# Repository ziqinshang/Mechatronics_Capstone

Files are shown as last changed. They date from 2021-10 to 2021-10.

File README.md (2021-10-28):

# Mechatronics_Capstone
## Overview
### This is a 4th year mechatronics engineering capstone project, The function of the device is to autonomously navigate a tomato or cherry tomato in greenhouse, and identify, pick, and collect tomatoes. This task was decomposed into several subsystems, navigation, image processing and robotic manipulation.
## Prototyping in Solidworks
CAD1
CAD2
## Frame Structure
Frame Structure 1
Frame Structure 2
## Manipulator Structure
Manipulator Structure
#### Note
#### Due to COVID-19 pandemic, several components necessary to finalize the development of the device were not fabricated resulting in a less-than-fully-functional prototype despite promising test data.
#### Group Effort
#### Credit: Alexander Cleator,Mingyang Xu, Qi Qi

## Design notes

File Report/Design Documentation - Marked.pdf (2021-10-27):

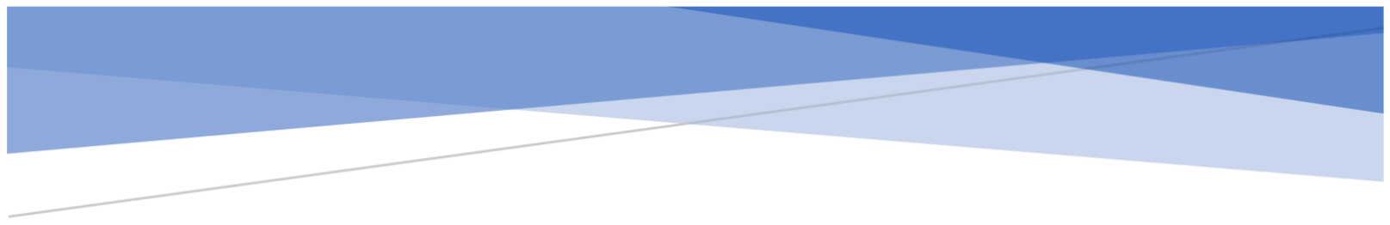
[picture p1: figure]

# FRUIT PICKING ROBOT FINAL DESIGN DOCCUMENTATION

## Group 7

Submitted: Feb 25, 2020

Prof. A. Samani

Alexander Cleator
Ziqin Shang
Qi Qi
Mingyang Xu

FRUIT PICKING ROBOT FINAL DESIGN DOCCUMENTATION | 1

## Table of Contents

# Part1: Design Analysis

## Frame Analysis

The frame is made from extruded 1060 aluminum alloy beams with following material

properties found on CES 2019:

Table 1: 1060 Aluminum Properties

1060 Aluminum is a strong, lightweight material that suitable for various of applications, in this

application, the strength of aluminum fulfilled the design requirement of supporting approximately 5kg of fruit and the 10kg mass of the robot. An FEA analysis was

conducted with a loading scenario of 100N distributed force on the base plate, a fine mesh was used in

this analysis. The results of the FEA analysis are shown in the following figures.

Figure 1: Von Mises Stress

It was found that the maximum Von Mises stress occurs on the contact edge of the plate and

the frame, which is 2.057 MPa, the yield strength of 1060 aluminum is approximately 160 MPa,

indicating no risk of failure by yielding.

The resultant displacement from the same analysis is shown below; it was found that the

maximum displacement of 0.03mm occurred along the center line of the plate.

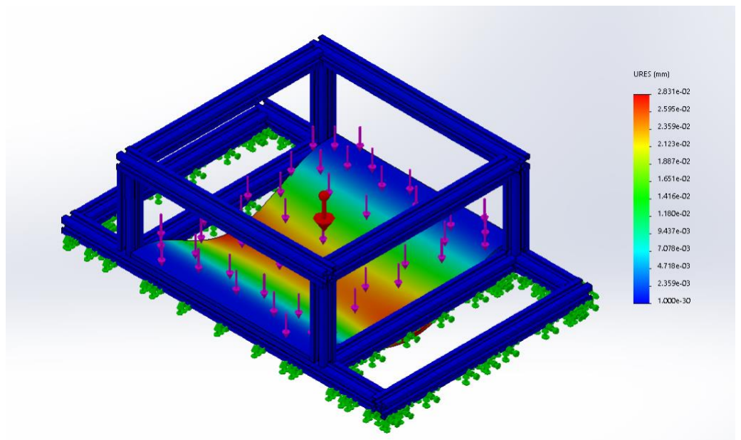
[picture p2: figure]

Figure 2: Deflection

## Motor analysis

By estimating the mass of the robot to be 10kg, a normal force of 24.5N can be applied

to each of the four wheels. Assuming the frictional coefficient between the wheels and the

ground is 0.6, a frictional force of 14.7N must be overcome. Based on Newton’s second law, a

net force of 1N must be applied to allow the 10kg device to accelerate at a rate of 0.1 m
s

2

Disregarding the moment of inertia of the wheel (as it was determined to be

inconsequential), the required torque can be calculated as follows:

τ = F x r = (15.7N) x (0.09m) = 1.41 Nm

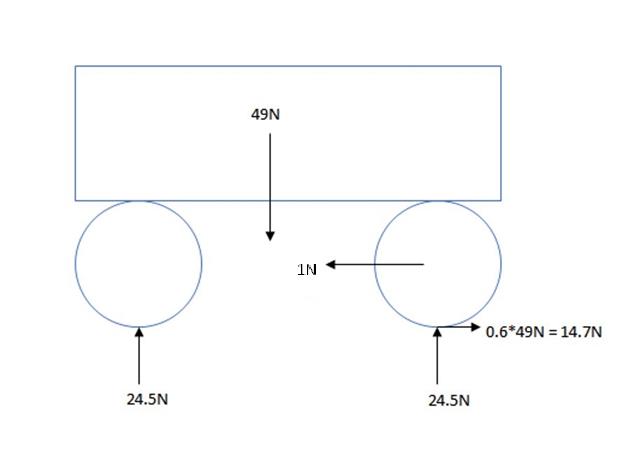
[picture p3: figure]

Figure 3: Chassis Static Force Analysis

Equating the applied force and friction, the required torque for continuous velocity can be

determined as follows.

τsteady state = Ffriction × rwℎeel = 14.7N × 0.09m = 1.32Nm

By estimating the operational speed of 0.5m
s

, the required rotational speed can be calculated

using the diameter of the wheel and speed of the robot:

circ. = πd = 0.18m x π = 0.565m

f =

v
circ

. =

0.5m
s
0.565m

= 0.884 Hz

frpm = 60f = 60(0.884) = 53 rpm

Considering the limited budget, a brushed DC motor is the optimal solution.

In this application, a gearbox is required because of the high speed, low torque direct output

from the motor.

Based on the specification that the selected motor must have a stall torque under 1.4 Nm and a

rated torque ideally as close as possible to 1.3Nm to maximize mechanical efficiency, a gearbox motor

with the following properties was selected.

Table 2: DC Motor Properties

Voltage | No-load speed | Rated speed | Rated torque | No-load current | Rated current | Stall current
24V DC | 325±30 RPM | 230 ± 20 RPM | 1.324N.m | 0.3A | 2.3A | 7A

The motor has an integrated 1:27 gear reducer, which amplifies the rated torque from 50mNm

to 1.324Nm that will fulfill the design requirement. A CNC machined steel shaft mount with an

integrated bearing was also purchased to mount the motor on the chassis. A 180mm diameter wheel

with aluminum wheel hub and rubber tire will be attached to the motor assembly.

The motor can be controlled using pulse width modulation, after a series of tests, a 15VDC

supply, operating at a 30% duty cycle could achieve the specified rate of 0.5 m
s

, a peak speed of 2.7m
s

was

observed during testing, which would be implemented if not for safety considerations. For this device,

rear differential steering was used due to the potential for zero-turn-radius steering. After completing

the concept generation and selection phases of the design development, construction began on both

a physical prototype and a Solidworks assembly to model the completed concept.

## Navigational System analysis

The navigational system uses an 8-bit hall-effect based magnetic line tracker and a 1.5-inch

magnetic strip. The magnetic tape is to be adhered to ground and line tracking sensor will detect

the horizontal relative location of the tape. By inputting the location information into a microprocessor

and using if-then logic, the speed of the two motor can be effectively controlled.

The magnetic sensor communicates serially based on MODBUS-RTU communication protocol or

as well as outputting the states of each of the hall-effect sensors NPN open-drain configurations. After

having difficulty establishing communication with the sensors MODBUS, tracking was achieved by

polling each of the sensors independently. Using the internal pull-up resistors in the

microprocessor, this information can be read directly through corresponding digital pins. After

processing, the microprocessor outputs a 5V PWM signal, which is amplified to a nominal voltage using

an integrated motor driver.

After a series of tests with different duty cycles and nominal voltages, following test results were

measured.

Table 3:Driving Speed Testing

Nominal Voltage | PWM ratio | Speed
10V | 30% | 0.3m/s
10V | 80% | 0.85m/s
15V | 30% | 0.5m/s
15V | 60% | 1m/s
24V | 30% | 0.8m/s
24V | 100% | 2.7m/s

Based on the test results, it was found that the robot can travel at a maximum speed of 2.7m
s

. By

varying the nominal voltage and duty cycle, the speed of robot can vary from 0.3 m
s

to 2.7 m
s

. The device

was unable to drive if the nominal voltage applied was less than 10V irrespective of duty cycle, voltages

above 24V were not tested to avoid potential damage to the motors being tested.

## 5 Degree of Freedom Manipulator

The manipulator operates using open loop controllers for each of the joints, which were coded

by the manufacturer. There are unfortunately no feedback sensors integrated into the manipulator as

shown in the manipulator’s owner manual and communication protocol. This resulted in observable

steady-state error in the z-direction when operating autonomously. After initial testing each joint was

tested to move from -90⁰ to 90⁰ in 1 second with zero observable overshoot. From the appearance of

the motion, the manipulator appears to use a cubic polynomial segmentation algorithm, however this is

speculation.

The manipulator has a reachable workspace consisting of a dome with a radius of 36cm

centered at a height of 9cm above the platform it is attached to.

### Forward Kinematics

To model the manipulator, both forward and inverse kinematic models were generated. The

forward kinematics were determined based on the following DH parameters, from which a series of

transformation matrices were calculated for each of the joint locations. The theta values used were

adjusted such that the commanded angles inherently programmed into the controller matched the

measured joint angles observed. Based on the following parameters an accurate model of the

manipulator kinematics was generated using MATLAB.

Table 4: DH Parameters

I | αi-1 | ai-1 | di | Θi
1 | 0 | 0 | 0.09 | Θ1 – π/2
2 | 0 | 0 | 0 | Θ2 – π/2
3 | -π/2 | 0.11 | 0 | Θ3
4 | 0 | 0.09 | 0 | Θ4
5 | 0 | 0.16 | 0 | 0

### Inverse Kinematics

The inverse kinematics of the manipulator were determined using an iterative algorithm called

FABRIK, Forward and Backwards Reaching Inverse Kinematics developed at the Department of

Engineering at Cambridge University, Cambridge, UK. The algorithm is best demonstrated in the

following Figure 4 . This method is far simpler than others used as it does not require matrix

manipulation, instead using simple geometry. This algorithm operates by positioning the end-effector at

the desired positionFigure 4 (b) , drawing a line between that position and the next joint n-1, positioning

joint n-1 a distance equal to the length of the link away from joint n along that line Figure 4 (c),

and repeating for the remaining jointsFigure 4 (d). Then, the base joint is placed at its proper location Figure 4 (e). The same process repeats propagating outwards from the base towards the end

effector. This cycle repeats until the base is located at its appropriate location and the end-effector is

close enough to its desired position to be considered acceptable Figure 4 (f). Testing in MATLAB resulted

in the end-effector being located within 0.1mm from the desired position, although higher accuracy

would be possible with more iterations.

This algorithm works very well in solving planar manipulators; however, a slight modification

was required to allow the manipulator to accurately model the manipulator used which is a planar

manipulator with a rotating base. Simply using the coordinate frame of the base rather than the

universal frame in this analysis resolved this issue. The code implementing this process, is also shown in

the following section, with the joint numbering reversed to correspond with the indexing used by

the manufacturers’ controller.

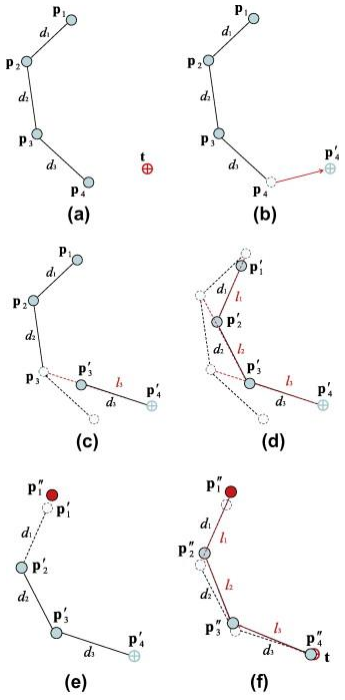
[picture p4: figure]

Figure 4: FABRIK Illustrated

The resolution of the manipulator is less precise than can allow for the 0.1mm accuracy

determined by the FABRIK algorithm. Each joint has a resolution of 0.18⁰, which, during testing

corresponded to an accuracy of ±0.5 cm in the x and y directions. This is also due to inherent error in

the controller provided, which does not appear to account for the weight of the manipulator based

on the observed steady state error in the z direction.

### End-effector Position Testing

The purpose of this test was to verify that the position of the end-effector commanded to the

manipulator matched with that being observed through measurement. This testing was to ensure that

the manipulator with the attached cutting head would be able to move to the desired

location to effectively cut the tomato from the vine.

During testing, the servo in joint 4 stopped working. It would not move under any applied load,

only operating under no-load conditions. As a result, the accuracy was greatly impacted as

the manipulator being used effectively had three degrees of freedom. This failure also prevented the

manipulator from operating within a 18cm dome centered on the base of the manipulator. The test

results of commanding a series of positions are as follows.

Table 5: Left/Right Sweep

Commanded Position | Actual Position
25 | 20 | 20 | 25 | 20 | 5
20 | 20 | 20 | 20 | 20 | 15
25 | 20 | 20 | 25 | 20 | 20
10 | 20 | 20 | 10 | 20 | 20
-10 | 20 | 20 | -10 | 20 | 20
-20 | 20 | 20 | -20 | 20 | 15
-25 | 20 | 20 | -25 | 20 | 5

Table 6:Forward/Back Sweep

Commanded Position | Actual Position
0 | 0 | 45 | 0 | 5 | 40
0 | 10 | 30 | 0 | 12 | 25
0 | 15 | 30 | 0 | 15 | 25
0 | 20 | 30 | 0 | 20 | 25
0 | 25 | 30 | 0 | 25 | 30
0 | 30 | 30 | 0 | 30 | 20
0 | 35 | 15 | 0 | 35 | 10

The x/y coordinates commanded were consistently accurate, however the measured z position was

consistently less than the commanded position. This is likely a control issue, not accounting for the

weight of the manipulator as the servos are not at their mechanical limits for any of the commanded

positions. Furthermore, the manipulator has no integrated feedback devices, resulting in open loop

control. This Prevents any sort of effective control without making significant modifications to the

construction of the manipulator.

## Manipulator Power Requirements

Table 7: Observed Power Requirements

Required Voltage | 7.5V
Peak Current (during acceleration) | 2.0A
Steady State Current (extended reach) | 0.35A
Stead State Current (upright rest position) | 0.2A

Based on the average AA battery, the battery pack of 5 AAs in series has a total 7.5V and a total

capacity of approximately 2500 mAh. Assuming an average current of 0.3A, the battery pack

should last approximately 8 hours before needing to be replaced or recharged. This battery life could be

extended by placing multiple battery packs in parallel, or by using higher capacity lithium-ion batteries.

However, for the purposes of a prototype, this was not attempted. For the final design, a single battery

is to be used, along with a voltage regulator as having multiple batteries of different voltages is both

redundant and poor design.

## Tomato Recognition

In this project, machine vision is used to recognize tomatoes from complex backgrounds and

return cartesian space information to robotics arm kinematics software for further processing. In

completed design, the tomato recognition software would be fully integrated with ultrasonic and

robotics arm kinematics to decide the movement of robotics arm.

The workflow of object recognition in this application is represented below:

Figure 5: Segmentation Algorithm

Because the algorithm is processing live video, the processing time for each frame must be less

than the capture frame rate. The decision-making process also needs to be aware of the response time

of the robotic arm and cutting action. The code implemented was developed using Matlab’s advanced

image processing toolbox and fast development nature. In production, the code will be ported to

OpenCV. Current code written on Matlab attempts to utilize vectorization, memory pre-allocation and

parallel processing to increase speed.

### Input and Connection

Using Matlab Image Acquisition toolbox and standard ‘winvideo’ hardware adapter. Color space

is set to RGB, resolution is set to 640x480 to reduce processing time. The capture framerate is set to 10

fps as it is fast enough for this application.

First, the RGB channels are combined into grayscale. Since the grape tomatoes are saturated red

with a mix of green, brown (red + green) and blue-sky background, we decided to use a linear algorithm

that promotes red and demotes green and blue to create the grayscale image. Grayscale=3*red

channel-2*(blue channel+ green channel).

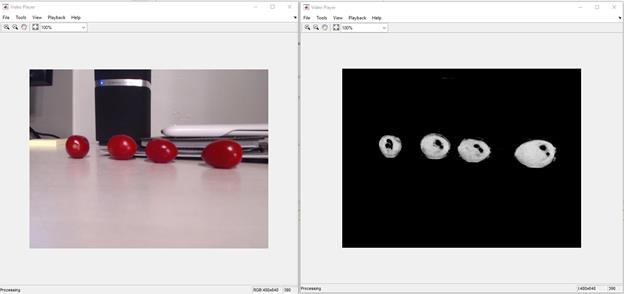
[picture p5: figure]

Figure 6: Initial Grayscale Results

Notice on the image, the holes inside the tomatoes are from overexposure areas due to the

point light in the test environment. Filling the contour is required in later processing. To get a cleaner

image and fill the hole, morphological reconstruction is used on the image to fill the small gaps and

holes.

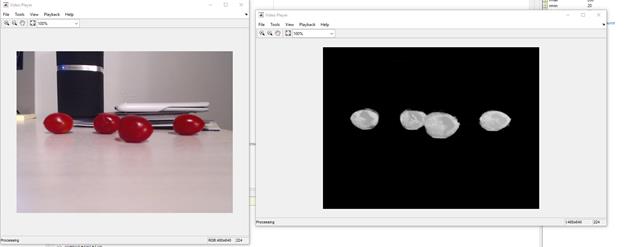
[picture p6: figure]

Figure 7: Morphologically Reconstructed Segmented Tomatoes

Each tomato is separated based on its position relative to the surrounding area. The top location of the

tomato is added to location of the end-effector and then returned as the output of the function.

## Emergency Stop Voice Recognition

As this robot is considerably dangerous, safety is an important consideration throughout the

devices’ development. When the user is close to the robot and they feel they are in danger of the

robot’s movement, for example he falls by accident in front of the robot or the robot is out of control. In

these scenarios, the user can yell “Stop!” out loud. The microphone on the robot is constantly listening

to the surrounding voice, it will capture the signal and compare the signal to the trained neural network

based on TensorFlow and act accordingly. The voice recognition system consists of two parts: a

preliminary band-pass filter and a trained neural network model.

### Band-pass filter

3 different “stop” voice samples by different people are recorded and analyzed.

Their frequency and spectrographs are represented below:

Figure 8: Test 1: Frequency and Spectrograph

Figure 9:Test 2: Frequency and Spectrograph

Figure 10: Test 3: Frequency and Spectrograph

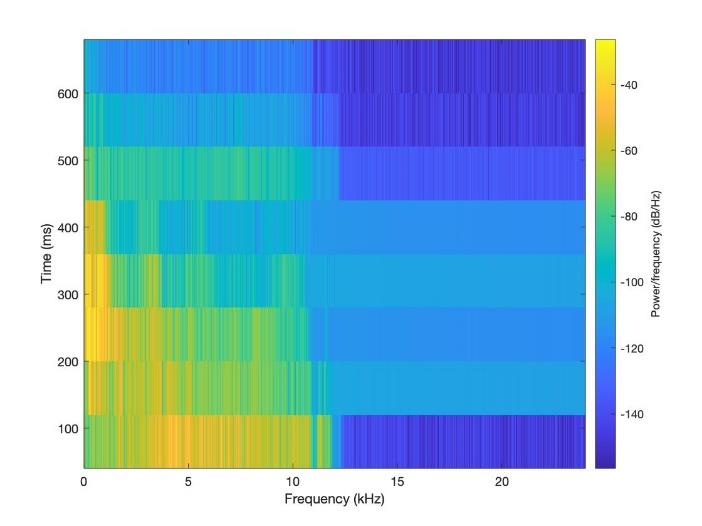
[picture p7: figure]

From the graph, most power of the “s” sound ranges between 5kHz to 8kHz, “top” sound ranges

below 400Hz and above 3kHz.

Based on the characteristic of “stop” sound, a Hamming windows FIR 400Hz-8kHz passband filter is

implemented to reduce noise.

### Neural network model

The neural network model is based on a Deepspeech model retrained with a focus on simple

word commands such as “stop”. The databases used include: LibriSpeech, Voice Commands Dataset,and

my owned recorded voices.

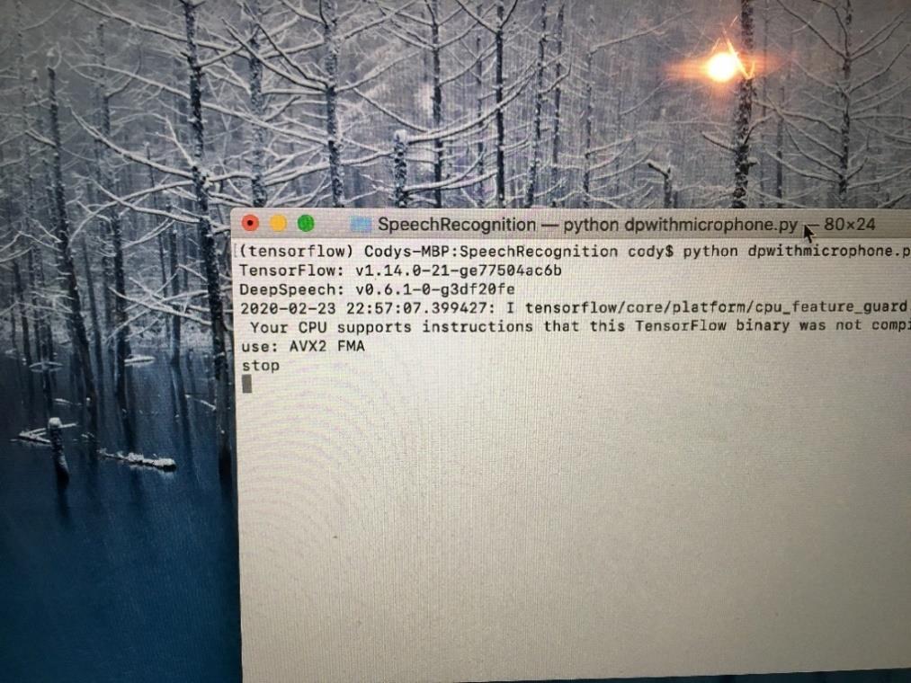
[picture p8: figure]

# Part 2: Detailed Design Documentation

## Manipulator Code

The following are a series of scripts that are command the robot to move to a specified location,

these scripts are triggered by the image processing code determining the location of a tomato. The

manipulator moves to that location, closes the gripper (cutting the vine), reopens it, then returns to its

original position until the script is called again.

## Serial_Comm.m

This script initializes the device, determines the required joint angles to move the end-effector to a

desired location in cartesian coordinates, then executes those same joint movements.

clc
clear
pause on
%Reset the device before initialziing communications instrreset
s = serial('COM5');
s.baud = 9600;
fopen(s);
s;

%Determine the required joint angles and write them to the manipulator %sequentially
resetServo(s)

Joint = invKinFcn(tomX;tomY;tomZ]) MoveAllServo(s,1500,joint(1),joint(2), joint(3), joint(4),1500,1500) Pause(1.5);
MoveAllServo(s,1500,joint(1),joint(2), joint(3), joint(4),1500,2000) Pause(1.5);
MoveAllServo(s,1500,joint(1),joint(2), joint(3), joint(4),1500,1500)

resetServo(s)

## MoveServo.m

This script moves a single servo to a specified position using serial communication. It first converts the

desired position from degrees to a position value that can be interpreted by the manipulator before

separating bother the position and time values into 16-bit unsigned integers and writing those values to

the manipulator.

function [] = moveServo(device,ServoID,Time,Position)

% Commands a servo to move to a specified position in a specified time %Linearize the position in degrees to an ADC value to be sent to the %manipulator
if ServoID == 6
outPosition = -11.111*Position + 1700;

end
if ServoID == 5
outPosition = 11.111*Position + 1733.3; end
if ServoID == 4
outPosition = 11.71*Position + 1151.5; end
if ServoID == 3
outPosition = 10.033*Position + 1566.4; end
if ServoID == 2 || ServoID == 1 outPosition = Position;
end

buf(1) = uint8(hex2dec('55')); buf(2) = uint8(hex2dec('55')); %length
buf(3) = uint8(hex2dec('08')); %command
buf(4) = uint8(hex2dec('03')); %# of servos to be controlled buf(5) = uint8(1);
% t
buf(6) = uint8(Time & 255); buf(7) = uint8(floor(Time/16/16)); %sevo ID
buf(8) = uint8(ServoID);
%Servo position
buf(9) = uint8(outPosition & 255); buf(10) = uint8(floor(outPosition/16/16));

%Write buffer to the manipulator fwrite(device,buf)

Linearization is achieved by measuring the joint angle of each of the servos in degrees and

plotting that against the digital value commanded to achieve that position. A linear regression was

calculated, and the corresponding equations were used to control the manipulator.

Joint 6 | | Joint 5 | Joint 4 | | Joint 3
Deg | ADC | Deg | ADC | Deg | ADC | Deg | ADC
90 | 700 | -90 | 700 | -45 | 700 | -90 | 700
-90 | 2700 | 0 | 1800 | 0 | 1050 | 0 | 1500
| | 90 | 2700 | 130 | 2700 | 110 | 2700

## InvKinFcn.m

This function is a modified implementation of the FABRIK algorithm (Forward and Backwards

Reaching Inverse Kinematics). This technique was published in a 2011 issue of the Graphical Models

journal and was developed by Andreas Aristidou and Joan Lasenby at the Cambridge University

Department of Engineering. This algorithm was modified to be used for the planar manipulator

implemented by the fruit picking robot by rotating the coordinate system attached at the base of the

robot to match the universal coordinate system.

function [ theta ] = invKinFcn( t )
%Inverse Kinematics function using FABRIK: Position control only p0 = [0;0;0.09];
p1 = [0;0;0.09];
p2 = [0;0;0.09];
p3 = [0;0;0.29];
p4 = [0;0;0.29];
p5 = [0;0;0.29];
p6 = [0;0;0.45];
p = [p0,p1,p2,p3,p4,p5,p6];

%define link lengths, d2, d5 defined as non-zero to avoid signular division %by zero error
d1 = 0.09;
d2 = 0.0001;
d3 = 0.29;
d4 = 0.0001;
d5 = 0.0001;
d6 = 0.16;

%rotate frame by t1 to create planar problem
t6 = atan2(t(2),t(1));
T01= [cos(t6), -sin(t6),0,0; sin(t6),cos(t6),0,0;0,0,1,0; 0,0,0,1];

%define target and rotate intitial joint positions to new plane target = T01*[t;1];
p1 = T01*[p1;1];
p2 = T01*[p2;1];
p3 = T01*[p3;1];
p4 = T01*[p4;1];
p5 = T01*[p5;1];
p6 = T01*[p6;1];

%simplify position vectors to x/y for 2d plotting target = target(2:3,1);
p1 = p1(2:3,1);
p2 = p2(2:3,1);
p3 = p3(2:3,1);

p4 = p4(2:3,1);
p5 = p5(2:3,1);
p6 = p6(2:3,1);

p = [[0;0.09],p1,p2,p3,p4,p5,p6];

%distance between joints
d = zeros(2:6);
dMag = zeros(6,1);
for i = 1:6
d(:,i) = p(:,i+1) - p(:,i); dMag(i) = sqrt(d(1,i)^2 + d(2,i)^2);

if dMag(i) == 0
dMag(i) = 0.0001;
end
end
dTarget = sqrt(target(1)^2 + target(2)^2);

%Determine if the target is withing reach if dTarget > (d1 + d2 + d3 + d4 +d5 +d6) fprintf('%s\n','Target out of reach') else
fprintf('%s\n','Target in reach')

diffMag = 1;

while diffMag > 0.0001
b = p(:,1);
p(:,7) = target;

for i = 6:-1:1
%fprintf('%s\n','forward reach') r(:,i) = p(:,i+1) - p(:,i); rMag(i) = sqrt(r(1,i)^2 + r(2,i)^2);

if rMag(i) == 0
rMag(i) = 0.0001;
end
lambda(i) = dMag(i)/rMag(i);
p(:,i) = (1 - lambda(i))*p(:,i+1) + lambda(i)*p(:,i); end

p(:,1) = b;

for i = 1:6
%fprintf('%s\n','backwards reach') r(:,i) = p(:,i+1) - p(:,i); rMag(i) = sqrt(r(1,i)^2 + r(2,i)^2);

if rMag(i) == 0
rMag(i) = 0.0001;
end lambda(i) = dMag(i)/rMag(i);

p(:,i+1) = (1 - lambda(i))*p(:,i) + lambda(i)*p(:,i+1); end

diff = p(:,7) - target;
diffMag = sqrt(diff(1)^2 + diff(2)^2); end
end

zMatrix = zeros(3,7);
zMatrix(2:3,:) = p;

R01 = T01(1:3,1:3);

jointPos = zeros(3,7);
for i = 1:7
jointPos(:,i) = R01'*zMatrix(:,i); end

r = zeros(2,6);
rMag = zeros(1,6);
for i = 1:6;
r(:,i) = p(:,i+1) - p(:,i); rMag(i) = sqrt(r(1,i)^2 + r(2,i)^2);

if rMag(i) == 0;
rMag(i) = 0.0001;
end
end

%determine required joint angles using atan2 p;
pGood(:,1) = p(:,1);
pGood(:,2) = p(:,4);
pGood(:,3) = p(:,5);
pGood(:,4) = p(:,7);

dx(1) = pGood(1,2) - pGood(1,1); dx(2) = pGood(1,3) - pGood(1,2); dx(3) = pGood(1,4) - pGood(1,3);

dy(1) = pGood(2,2) - pGood(2,1); dy(2) = pGood(2,3) - pGood(2,2); dy(3) = pGood(2,4) - pGood(2,3);

t5 = atan2(dx(1),dy(1));
t4 = 0;
t3 = atan2(dx(3),dy(3)) - t4 - t5;

%output resultant angles, made negative to counteract opposite direction of %frame of reference Z vector
theta = [rad2deg(t6),rad2deg(t5),rad2deg(t4),rad2deg(t3)];
end

## Chassis Navigation Code

The following code implements differential steering navigation based on the output of the line

tracker sensor attached to the front of the device. If the device begins to turn to the left, the left wheel

drives faster to ensure proper tracking, the same for the left wheel. The entire process is shown in the

following flowchart.

int PWM1 = 10;

int INA1 = A2;

int INB1 = A4;

int PWM2 = 11;

int INA2 = A3;

int INB2 = A5;

int s1 = 0;//initial values for each pin on sensor

int s2 = 0;

int s3 = 0;

int s4 = 0;

int s5 = 0;

int s6 = 0;

int s7 = 0;

int s8 = 0;

int stopPin = 12;

void setup()

{

Serial.begin(9600);

pinMode(PWM1, OUTPUT);

pinMode(INA1, OUTPUT);

pinMode(INB1, OUTPUT);

pinMode(PWM2, OUTPUT);

pinMode(INA2, OUTPUT);

pinMode(INB2, OUTPUT);

pinMode(stopPin, INPUT);

for (int i = 2; i <= 9; i++) pinMode(i, INPUT_PULLUP); // set pin 2-9 to input with pull up

}

void loop()

{

s1 = digitalRead(2);

s2 = digitalRead(3);

s3 = digitalRead(4);

s4 = digitalRead(5);

s5 = digitalRead(6);

s6 = digitalRead(7);

s7 = digitalRead(8);

s8 = digitalRead(9);

stopFlag = digitalRead(stopPin);

digitalWrite(INA1,LOW); //motor 1 and 2 turning forward

digitalWrite(INA2,LOW); //motor 1: left motor

digitalWrite(INB1,HIGH); //motor 2: right motor

digitalWrite(INB2,HIGH);

if(s1==1 && s2==0 && s3==0 && s4==0 && s5==0 && s6==0 && s7==1 && s8==1){

displaysensorvalue(s1,s2,s3,s4,s5,s6,s7,s8);

Serial.print("Going Straight");

analogWrite(PWM1,75);

analogWrite(PWM2,75);

}

if(s1==1 && s2==0 && s3==0 && s4==0 && s5==0 && s6==0 && s7==0 && s8==1){

displaysensorvalue(s1,s2,s3,s4,s5,s6,s7,s8);

Serial.print("Going Straight");

analogWrite(PWM1,75);

analogWrite(PWM2,75);

}

if(s1==1 && s2==1 && s3==0 && s4==0 && s5==0 && s6==0 && s7==0 && s8==1){

displaysensorvalue(s1,s2,s3,s4,s5,s6,s7,s8);

Serial.print("Going Straight");

analogWrite(PWM1,75);

analogWrite(PWM2,75);

}

if(s1==1 && s2==0 && s3==0 && s4==0 && s5==0 && s6==0 && s7==1 && s8==1){

displaysensorvalue(s1,s2,s3,s4,s5,s6,s7,s8);

Serial.print("Going Straight");

analogWrite(PWM1,75);

analogWrite(PWM2,75);

}

if(s1==1 && s2==1 && s3==0 && s4==0 && s5==0 && s6==0 && s7==0 && s8==0){

displaysensorvalue(s1,s2,s3,s4,s5,s6,s7,s8);

Serial.print("Turing Left slightly");

analogWrite(PWM2,70);

analogWrite(PWM1,80);

}

if(s1==1 && s2==1 && s3==1 && s4==0 && s5==0 && s6==0 && s7==0 && s8==0){

displaysensorvalue(s1,s2,s3,s4,s5,s6,s7,s8);

Serial.print("Turing Left moderately");

analogWrite(PWM2,60);

analogWrite(PWM1,90);

}

if(s1==1 && s2==1 && s3==1 && s4==1 && s5==0 && s6==0 && s7==0 && s8==0){

displaysensorvalue(s1,s2,s3,s4,s5,s6,s7,s8);

Serial.print("Turing Left intensely");

analogWrite(PWM2,50);

analogWrite(PWM1,100);

}

if(s1==0 && s2==0 && s3==0 && s4==0 && s5==0 && s6==0 && s7==1 && s8==1){

displaysensorvalue(s1,s2,s3,s4,s5,s6,s7,s8);

Serial.print("Turing Right slightly");

analogWrite(PWM2,80);

analogWrite(PWM1,70);

}

if(s1==0 && s2==0 && s3==0 && s4==0 && s5==0 && s6==1 && s7==1 && s8==1){

displaysensorvalue(s1,s2,s3,s4,s5,s6,s7,s8);

Serial.print("Turing Right moderately");

analogWrite(PWM2,90);

analogWrite(PWM1,60);

}

if(s1==0 && s2==0 && s3==0 && s4==0 && s5==1 && s6==1 && s7==1 && s8==1){

displaysensorvalue(s1,s2,s3,s4,s5,s6,s7,s8);

Serial.print("Turing Right intensely");

analogWrite(PWM2,100);

analogWrite(PWM1,50);

}

if((s1==1 && s2==1 && s3==1 && s4==1 && s5==1 && s6==1 && s7==1 && s8==1)||stopFlag == 1){

displaysensorvalue(s1,s2,s3,s4,s5,s6,s7,s8);

Serial.print("Vehicle Stopped,no signal detected");

digitalWrite(INA1,LOW);

digitalWrite(INB1,LOW);

digitalWrite(INA2,LOW);

digitalWrite(INB2,LOW);

}

delay(100);

}

void displaysensorvalue(int s1,int s2,int s3,int s4,int s5,int s6,int s7,int s8){

Serial.print(s1);

Serial.print(s2);

Serial.print(s3);

Serial.print(s4);

Serial.print(s5);

Serial.print(s6);

Serial.print(s7);

Serial.print(s8);

Serial.print("\n");

}

## Chassis and Manipulator Bill of Materials

## Navigation System Wiring Diagram

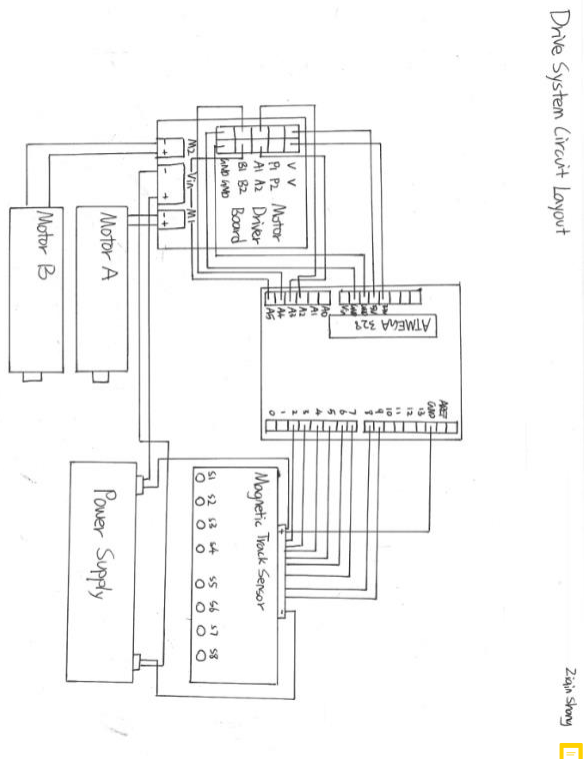
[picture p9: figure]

## Motor Driver Schematic

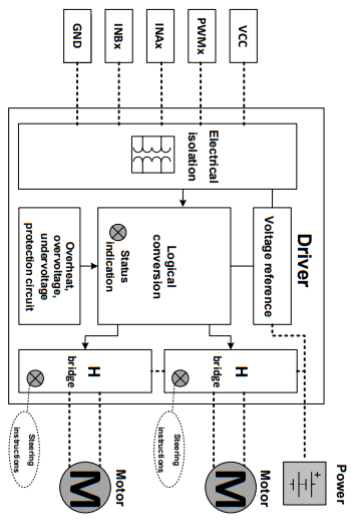
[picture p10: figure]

## Image Processing Code

%connecting hardware

vidinput=videoinput('winvideo',1,'MJPG_640x480');

%Configure the triiger mode to be manual, greadtly reduce the triiger time

%and overhead

triggerconfig(vidinput, 'manual');

%framerate

vidsrc=getselectedsource(vidinput);

vidsrc.FrameRate='10.0000';

%Video player object to display frame

disporiginal=vision.VideoPlayer;

disppros=vision.VideoPlayer;

%start video

start(vidinput);

tic

%variables delcared here for image processing

threshold=30;

%hough trasnfrom parametes

rmin=20; rmax=200;

%try to do vectorization to increase speed

for i=1:500

im=getsnapshot(vidinput);

disporiginal.step(im);

%split into rgb channels redchannel=squeeze(im(:,:,1));

greenchannel=squeeze(im(:,:,2));

bluechannel=squeeze(im(:,:,3));

%create binary image, mathematic operation 3R-G-B

impros=3*redchannel-2*(greenchannel+bluechannel);

%Median filter , default is 3x3 matrix

impros=medfilt2(impros,[2 2]);

%thresholding

impros=logical(impros-threshold);

%remove pixel groups that have less than 200 pixels in a group

impros=bwareaopen(impros,200);

%Currently don't need to close the boundary, it also results

%over-emerging of different obejcts

impros=imfill(impros,'holes');

%impros=bwconvhull(impros,'objects');

impros=logical(impros-threshold);

%define circle size to be 40:120

%[houghtranscenter,houghtransradi]=imfindcircles(impros,[rmin rmax],'ObjectPolarity','bright','Sensitivity',0.9);

%houghtranscenter=round(houghtranscenter);

disppros.step(impros);

end

%%%end task

timedur=toc;

eachframe=timedur/500;

stop(vidinput);

delete(vidinput);

clear vidinput;

## Emergency Stop Voice Recognition

from deepspeech import Model

import numpy as np

import speech_recognition as sr

beam_width = 500

micfs=16000

models_folder = 'models/'

model_name = models_folder+"output_graph.pbmm"

ds = Model(model_name,beam_width)

mic = sr.Microphone(sample_rate=micfs)

r = sr.Recognizer()

with mic as source:r.adjust_for_ambient_noise(source)

while True:

with mic as source:

audio=r.listen(source,phrase_time_limit=1.3)

audio = np.frombuffer(audio.frame_data, np.int16)

print(ds.stt(audio))

## Mechanical Drawings

The following are the mechanical drawings necessary to fabricate the device. Components such

as screws, nuts, washers etc were not drawn as they are standard components that would not need to

be fabricated by a manufacturer.

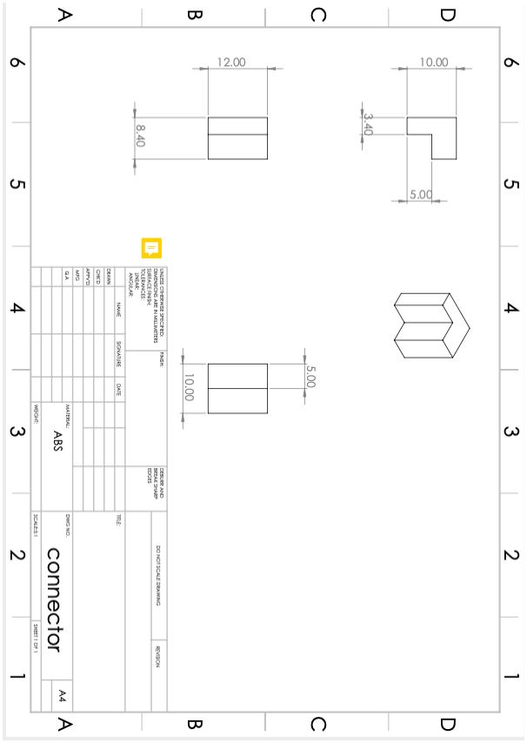
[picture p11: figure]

# Part 3: Prototype Structure, Fabrication Plan and Cost

## Prototype Functionality

The prototype constructed is as fully functional model of the finished design. It is a fully

autonomous device capable of following a magnetic strip, while picking cherry tomatoes. Each

subsystem - autonomous navigation, the robotic manipulator, image processing, and end-effector -

were developed relatively independently and integrated into a single system.

The navigation system integrated in the prototype uses an 8-bit magnetic line tracker that

responds based on the relative position of the tracker with the magnetic strip that it is following. Based

on the data provided by the sensor, differential steering is used to control the device accordingly. During

testing, this system proved to be very effective at the prescribed speed of 0.5m/s and was capable of

tracking curves with a radius of as low as 1m.

The manipulator was less effective as after purchase and implementation it was discovered that

it is only capable of open loop control, and that it was not possible to request the position of the

integrated servos to allow for closed loop control. As a result, steady state error was observed in the z-

direction as a result of the manipulators included controller not accounting for its own weight, rectifying

this issue was not possible with the included controller as the error was non-linear and could not be

calibrated out of the system.

Due to inefficient scheduling near the beginning of the course, the revised design of the end-

effector was not implanted as was originally intended, rather a modified version of the manufacturers’

gripper was used to cut the stem of the tomato vine. Unfortunately, the open loop control, and lack of feedback from the manipulator did not allow for successful implementation of the cutting mechanism

except for in a limited workspace where the moment generated by the weight of the arm is minimal.

The image processing however did work very well and was able to effectively return cartesian

coordinates for the centroid of the tomato, from which the stem could be cut above the tomato,

checking that no other tomatoes are being cut accidentally. During testing, image processing software

was shown to be able to identify tomatoes effectively, even if they were in front of each other, were

moving slightly, or were in front of a complex background. Some accuracy was lost if the tomatoes were

blocked by leaves or other foliage, as that influenced where the software identified to centroid to be.

## Manipulator Assembly Instructions

1. Attach one base LDX-218 servo mount to an upper base plate using four 10mm M3 screws and

four M3 nuts.

2. Attach the metal servo plate on a separate LDX-218 Servo to the lower base plate. Insert the

servo plate into the hole in the base plate and attach using four 10 mm 3M screws and four M3

nuts.

3. Position one large bearing between the upper base plate the lower base plate ensuring the M3

screw holes are aligned.

4. Connect the bearing, upper, and lower base plates using 15mm M3 screws and M3 nuts, tighten

to apply equal circumferential pressure to the bearing.

5. Align two base rings with the completed assembly such that the screw holes on the outer rings

align radially with the base plates. The outer rings should be covering half of the bearing both

above and below.

6. Connect the outer rings together using 12mm M3 screws and 15mm threader columns. Tighten

evenly around the circumference of the rings, to apply consistent pressure to the bearing.

7. Position a base ring with the screw threaded columns at the base of the assembly, connect

using 40mm columns.

8. Attach one LDX-218 Servo to the LDX-218 servo mount, aligning the driving plate with the

indentation on the mount, and attaching using three 5mm M2 screws.

9. Attach two large U brackets to each other using 10mm M3 Screws, aligning the center holes on

the base of each with each other.

10. Attach one end of the U bracket assembly to the assembled base and attach the other to the

driving plate of another LDX-218 servo.

11. Attach a small U Bracket to another large U bracket using 5mm 2M screws and 2M nuts similarly

to the large U brackets previously assembled.

12. Attach the small U bracket to the LDX-218 servo using 5mm 2M screws.
13. Attach two LDF-06 servo mounts together rotated 90⁰ relative to each other using 10mm 3M

screws and nuts.

14. To one side of the large U bracket in the previous assembly, attach the servo mount assembly

and small bearing such that the bearing is in the center hole of the large bracket.

15. Attach one LFD-06 servo to the servo mount using 10mm 3M screws and 3M nuts.
16. Attach the servo driving plate to the other side of the large bracket using 5mm 2M screws.
17. Attach a second LFD-06 servo to the available servo mount using 10mm 3M screws and 3M nuts.
18. Attach the gripper assembly to the driving plate of this servo.

## Gripper Assembly Instructions

1. Attach two servo mounting clips to opposite sides of the base plate using 10mm 3M screws.
2. Attach one driving gear and a spacer to the base plate using a 15mm 3M screw.
3. Attach one LDF-06 servo to the four mounting posts on the base plate. Attach a second driving

gear to the driving plate on the servo. The two driving gears should be level with each other.

4. Attach two grippers to the holes at the end of each other driving gears. Connect the driving

gear, and two grippers with a 15mm M3 Screw and M3 nut. Mirror this connection on the other

side of the mechanism.

5. Attach one link above the base plate, and a spacer and link below using a 15mm M3 screw. The

link above the base plate should be level with the driving gears.

6. Attach the opposite ends of the links to the gripper. One link above the two gripper pieces, and

one link below them. Connect the four components together using a 15mm M3 screw and M3

nut.

7. Repeat steps 5 and 6 on the opposite side of the mechanism.
8. Attach a single utility knife blade to the end of each of the grippers. Move the grippers manually

to ensure the blades pass each other closely.

## Chassis Assembly Instructions

1. Cut a series of 2020 extruded aluminum beams to the following lengths:
a. 450 mm (x2)
b. 300 mm (x2)
c. 260mm (x5)
d. 100mm (x4)
e. 95mm (x4)
f. 70mm (x4)
2. Connect two 450mm beams with a 260mm beam and fasten using 12mm M5 screws and corner

brackets

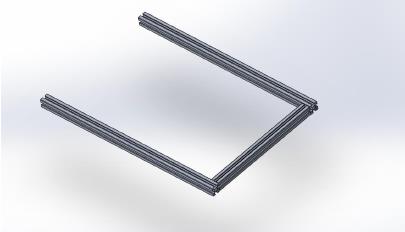
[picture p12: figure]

3. Insert two 260mm beams centered about the middle of the 450mm beam. Leave a space of

260mm between them.

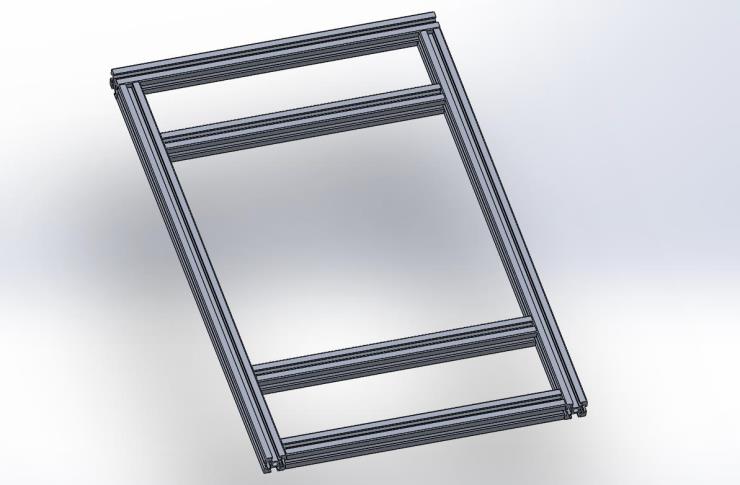
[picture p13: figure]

4. Close the opposite end of the frame using a 300mm beam, allowing this beam to overhang the

ends of the 450mm beams.

5. Install four 100mm beams at the corners of the inner 260mm square frame.
6. Install two 300mm beams on top of the 100mm beams, parallel to the 450mm beams already

installed.

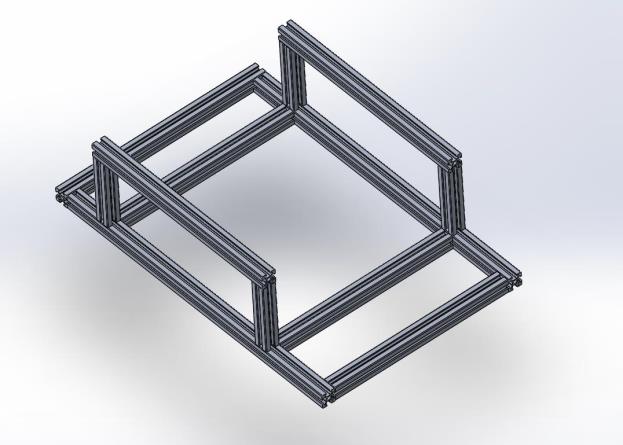
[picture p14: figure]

7. Connect two 260mm beams perpendicular to the 300mm beams, this completes a 300mm

square platform above the base of the frame.

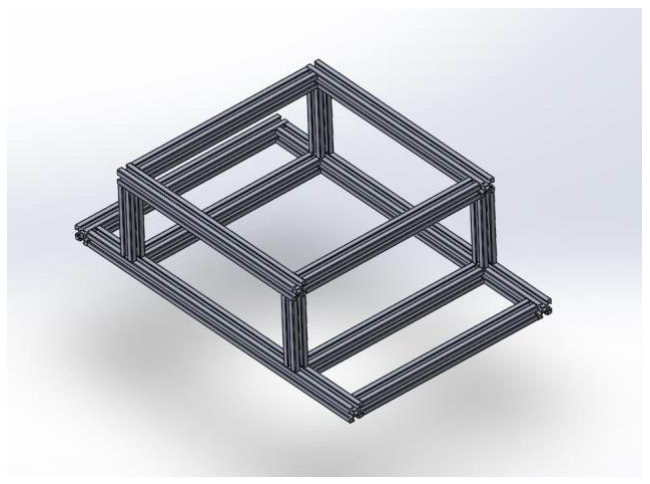
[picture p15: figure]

8. Attach two 95mm beams to the flat plate of each caster.

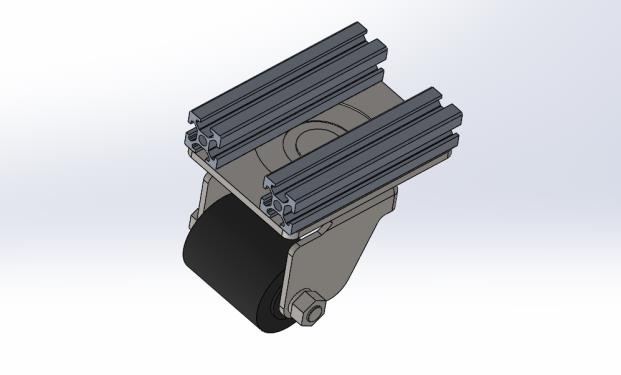
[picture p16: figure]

9. Attach two 70mm beams perpendicular to the 95mm beams to each caster.
10. Attach the caster assemblies to one end of the frame.

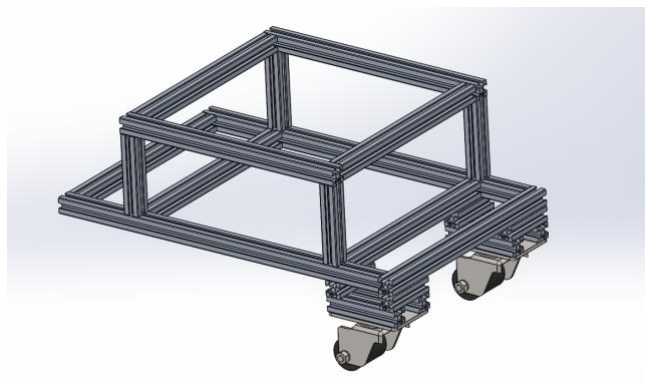
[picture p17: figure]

11. Attach the motor mounts to the frame using machine screws. Position the motor mount the

corner of the upper square frame.

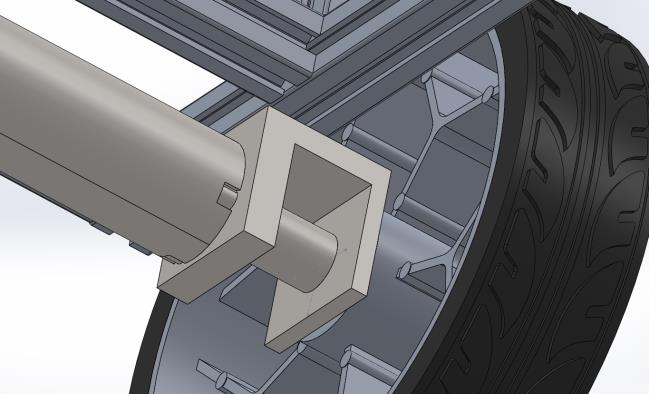
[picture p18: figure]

12. Attach two motor mounts to each of the 24V DC motors.
13. Press fit the wheels to the motor shaft, aligning the key and keyway on each.

14. Position the magnetic line tracker sensor mount in the center of the front of the frame.

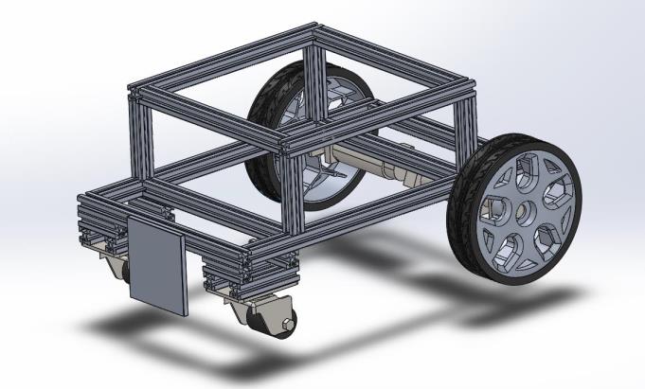
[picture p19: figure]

15. Attach the magnetic line tracking sensor to its mount using the appropriate holes.
16. Install the container base plate inside the square frame.

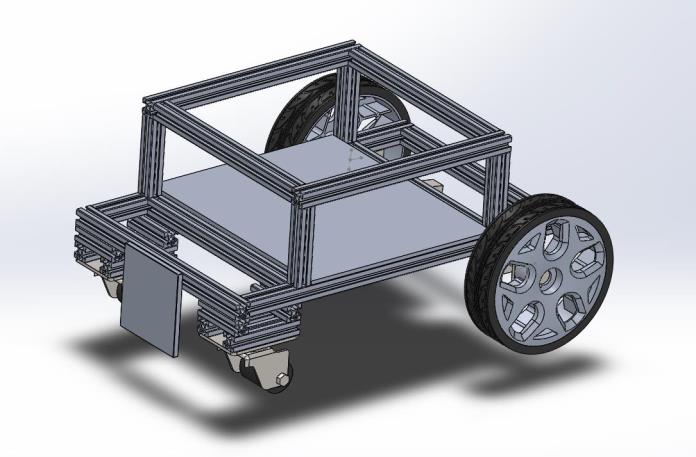
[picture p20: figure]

17. Install the acrylic side panels to the sides of the square frame. Ensuring the panel with the hole

is installed on one of the sides.

18. Attach the upper container plate using machine screws to the top of the square frame.

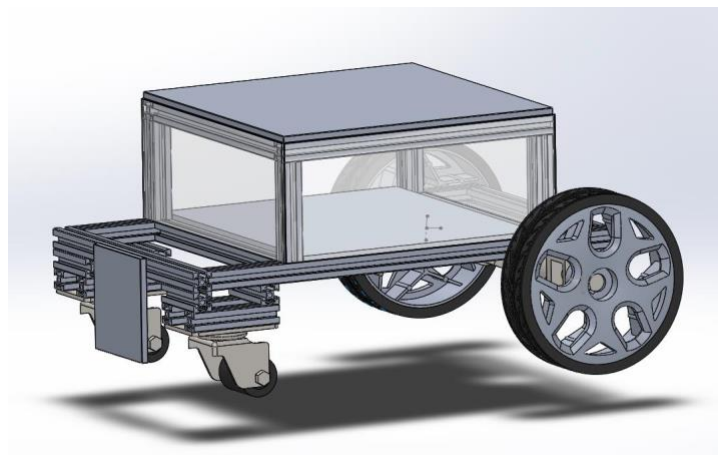
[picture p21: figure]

19. Attach the manipulator to the top of the container plate using locking nuts.

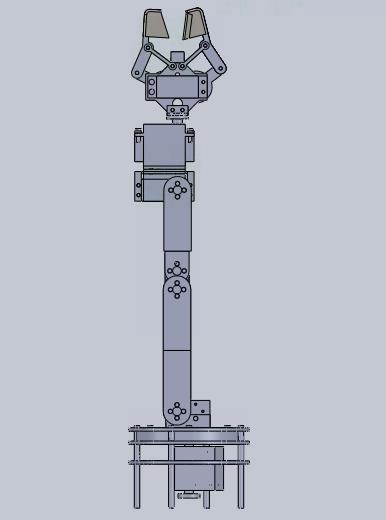
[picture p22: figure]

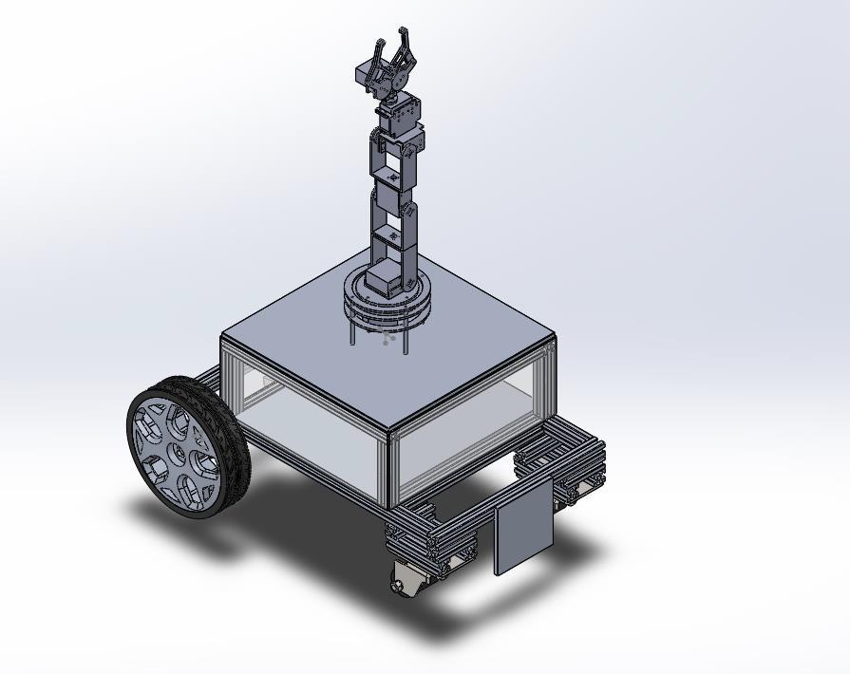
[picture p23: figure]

20. Mount the motor driver, microcontroller and battery above the 24V motors, and wire according

to the appropriate diagram.

21. Connect the flexible collection tube to the end effector collar using the previously attached L

bracket. Connect the opposite end of the tube to the hole in the side of the collection bin.

## Alternative Fabrication Options

In developing the prototype aluminum components were primarily used due to their light

weight and ease of availability. Furthermore, aluminum can easily be machined using the available

equipment in the Student Machine Shop. Steel was considered, however using a steel chassis would

have greatly increased its weight, which would negatively impact battery life.

The cost of the container could greatly be reduced by using a prefabricated container rather

than assembled panels. However, this predominantly only affected the prototype as the final design

(being mass produced) would be much cheaper due to the economies of scale in mass producing simple

plastic panels. Furthermore, in the final design acrylic is specified as the material to be used for the

panels, although polyethylene, polycarbonate or other plastics would function similarly. Acrylic was

chosen due to its properties as being very hard and tough, which allowed for vigorous testing and abuse

during the prototyping phase.

## Material Costs

The following table outlines a comprehensive, itemized invoice of the material costs associated

with the construction of the prototype and ultimately the final design of the fruit picking robot.

Item | Quantity | Unit Cost | Total Cost
Drive wheel | 2 | $18.63 | $37.26
Driven wheel | 2 | $12.61 | $25.22
8-Bit magnetic line tracking sensor | 1 | $55.51 | $55.51
BTN7971 motor driver | 1 | $24.09 | $24.09
MD36 35W 24V DC Motor with optical encoder | 2 | $73.92 | $147.84
Ultrasonic sensor | 1 | $1.32 | $1.32
Ultrasonic sensor mount | 1 | $0.56 | $0.56
24V to 5V voltage converter | 1 | $3.20 | $3.20
M5 washer | 50 | $0.02 | $1.00
M5-12 screw | 10 | $0.08 | $0.80

M5-14 screw | 10 | $0.09 | $0.90
M5 – 16 screw | 10 | $0.09 | $0.90
M5 nylon lock nut | 30 | $0.04 | $1.20
Aluminum beam corner bracket | 40 | $0.53 | $21.20
80cm 2020 aluminum beam | 10 | $1.67 | $16.70
5-DOF Manipulator and associated hardware | 1 | $165.29 | $165.29
Acrylic Panels | 4 | $1.10 | $4.40
100 mm flexible hose | 1 | $2.50 | $2.50
| | Total | $509.89

## Potential Cost Savings

Item | Cost | Savings
Reed sensor SPST | $18.00 | $37.51
24V 5300RPM DC motor | $25.84 | $96.15
Injection molded wheels | $10 | $24.25
Total Savings | | $156.11
Potential cost | | $353.78

As can be seen, the project did exceed the budget by $210, this could be addressed by using

single hall-effect sensors instead of the single integrated sensor, using a lower-powered motor instead

of the 24V motor specified and operating at a lower efficiency (sacrificing battery life), and at a higher

average voltage. Savings also could have been had on the driving wheels. The wheel specified are cast

aluminum, plastic wheels could have been used at the expense of durability. The reasons these changes

were not implemented were to both improve the quality of the finished design, ease maintenance, and

allow for easier testing and prototyping.

### Fabricated Prototype

Figure 11. Fabricated Chassis

Figure 12. Enlarged view of the magnetic Sensor

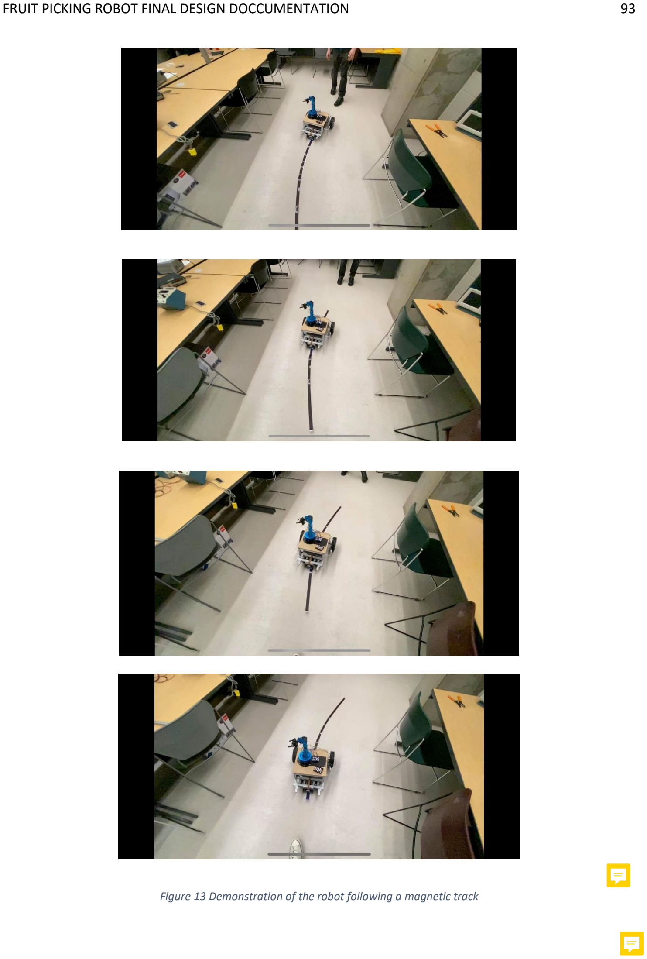
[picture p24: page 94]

Figure 13 Demonstration of the robot following a magnetic track

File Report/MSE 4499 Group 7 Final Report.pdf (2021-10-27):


## MSE 4499 — Mechatronic Design Project

# Fruit Picking Robot

by

Alexander Cleator

Ziqin Shang

Qi Qi

Mingyang Xu

Final Report

Faculty Advisor: Prof. L. Brown

Date Submitted: Friday April 3, 2020

Word Count: 7942

i

Contents

ii

iii

iv

v

Table of Figures

Figure 10: Steady-State Linear Speed Test Data Plotted with Linear Regression ........ 35

vi

Table of Tables

vii

Executive Summary

In this summative report, the entire design process is outlined and discussed for the

development of a fully autonomous tomato harvesting mobile robot to supplement a

substantial worker shortage in the agricultural industry. The function of the device is to

autonomously navigate a tomato or cherry tomato greenhouse, and identify, pick, and

collect tomatoes. This task was decomposed into several subsystems, navigation,

image processing, robotic manipulation, and the robot-tomato interface. Speed and

accuracy tests were conducted were conducted on the relevant systems which resulted

in the successful iterative development of these systems. Several comprehensive

progress reviews were conducted during which the current progress was discussed as

was suggestions for improvement including the switch from encoder-based navigation

to the use of an external sensor (such as a line-tracker). Each of the independent

subsystems were successfully developed, however due to current world events

(COVID-19 pandemic) several components necessary to finalize the development of the

device were not fabricated resulting in a less-than-fully-functional prototype despite

promising test data.

Introduction

In 2014, 26,400 agricultural jobs were unfilled according to a study published by

the Canadian Agricultural and Human Resources Council funded by the Government of

Canada’s Sectoral Initiatives program [1]. By 2025, this gap is expected to grow to

113,800. This labour shortage proliferates numerous costs in the agricultural industry,

with 55% of respondents claiming production delays, and lost revenue. Other attributed

costs include production losses, delayed or cancelled capital expansions, and overtime

costs. Aside from the lack of workers available, the same study continues to state that

finding quality workers is more important the quantity of applicants. Higher quality

workers can be defined as better skilled workers, who have a natural interest in their

work resulting in a lower turnover rate and a higher average quality of worker as skills

improve over time.


Figure 1: Labour Shortage Consequences

This large-scale labour shortage was estimated to cost farmers a total of $2.9

billion in lost revenue in 2017 according to the Labour Market Forecast to 2029, also

published by the Canadian Agricultural Human Resources Council. In 2019 Canada’s

agriculture sector lost $2.9 billion to lost sales because of this tremendous shortage, and that loss is predicted to grow further [2]. While harvesting labourers are only

predicted to make up 7% of the total labour gap, it is a repetitive, labour intensive task,

which pays poorly, and is critical to production. Regardless of the potential losses of an

unfilled management position, compared to an unfilled general labourer or harvester,

the loss that can be attributed to the shortage of harvesters can be conservatively

estimated to be at least 3% of the total loss across the agricultural industry. This

conservative estimate would suggest $90 million dollars in 2019 (likely more) can be

directly attributed to the lack of harvesting positions being filled. Consequently, 30% of

respondents stated that they considered overtime costs to be a direct result of the

labour shortage as well. Excessive overtime work often results in poor morale among

workers, high turnover rates, and poor-quality work [3] [4], which contributes back to the

previously stated results of extreme labour shortage. Automating harvesting positions

would address most of the above issues, while displacing a minimal number of

established jobs, and create new skilled jobs in the manufacturing and automation

servicing industries.

The proposed solution is to automate the agricultural harvesting process and

create a mechatronic device to identify and pick greenhouse tomatoes. This device

would be marketed towards small and medium sized farms, where it would be more

cost efficient to have the device work in relative isolation in comparison to large farms

with large crews where many people working together would be more efficient.

Furthermore, marketing to a smaller market could act as a pilot project, to test the

scalability of the concept.

Background Information

Current State of the Art

Automating the fruit picking process is not an entirely novel idea, several

prototypes of functional devices have been designed in the past, however they have

some critical errors that our team intends to address. It is important to first establish the

current state of the art regarding automating soft-fruit harvesting. The most notable

example is a very recent development by a UK start-up enterprise called Fieldwork

Robotics. Their device is capable of picking 1250 raspberries per hour compared

to 1875 a human could pick in that same time period [5]. Their robot uses template-

based image processing, and a vaguely described four-armed flexible robotic

manipulator. UK based media outlet Express covered the story, and in an interview

with Fieldworks’ robotics director Dr. Martin Stoelen, he stated “Different light

conditions, branches, [and] pests … have been the biggest challenges” in reference to

the sensitivity of the image processing methods to debris or partial occlusion of the

raspberries. To date, £672,000 ($1,142,000 CAD) have been invested in the project

[6]. This project is at the forefront of the current technological frontier regarding fruit-

picking automation, highlighting that image processing is the most challenging issue of

this endeavor.

In a similar article published in the Washington post, image processing concerns

are echoed as the device described is unable to differentiate between ripe, over, or

underripe fruit. While outlining the technological concerns regarding the image

processing issues, the article further references mechanical brutality towards produce.

The focus of the article however is on the social implications of automating fruit harvesting. There is a clear and obvious stigma towards automation as it is seen as a

replacement for human jobs (which to an extend is justified), however the benefits of

creating skilled positions are also discussed.

Both articles refer to similar primary problems, and several secondary ones. The

primary issues outlined are the image processing considerations, and the robot’s ability

to safely handle fruit without causing any damage. If a robot is unable to both identify

and safely pick fruit, it is essentially useless in this application. As our team lacks an

understanding of both the theory and application of advanced image processing

techniques such as template matching, for the sake of feasibility our device will locate

the centroid and outline of a color blob and cut a prescribed distance above the fruit.

The second problem of the safe handling of the produce is a much more feasible task.

The secondary problems include increasing the speed of the entire operation, ensuring

the device can navigate difficult terrain, and finally can operate outdoors.

Color Blob Image Segmentation

To effectively pick tomatoes off a plant, the tomato must be identified and located

using colour blob image processing techniques. This problem can be split into two


Figure 3: CIE LUV Colour Space | Figure 2:RGB Colour Space

distinct sub-problems. First, the tomato must be isolated from the background, second,

the tomato must be assigned a position in three-dimensional space to allow the robotic

manipulator to interact with it. Reviewing an IEEE published paper entitled “Color Blob

Segmentation by MSER Analysis” [7], color blob image segmentation requires four

steps.

First, a set of colour values to be segmented must be defined. Next, the image is

converted from RGB colour space (red-green-blue) to the CIE Luv colour space.

Next, the colour value of each pixel must be compared to those next to it. This is

achieved by defining a vector to each pixel with values L, u, and v from the Luv colour

space (µ), as well as a covariance matrix (Σ) based on Gaussian distributions to

determine the colour similarities between pixels. Using these matrices, the

Bhattacharyya distance (a quantitative value indicating the similarity of two pixels) can

be determined using the following relationship.

Equation 1: Bhattacharyya Distance

Finally, a list of Bhattacharyya pixel distances is created, and those beneath a

set sensitivity threshold are grouped to form the selected subregion of the image. This

process is typically completed by software included in most image processing

packages, and likely Matlab. However, it is important to understand the underlying

principles of image segmentation, to refine or develop an appropriate algorithm to

isolate tomatoes from their background.

Scope, Constraints, and Objectives

Scope

In order to ensure the completion of a functional device, the scope of the project will (in

some ways) be limited. This was primarily implemented during the development of

concepts, with an obvious example of this being the immediate elimination of any air-

borne or UAV (unmanned aerial vehicle) based solutions. These solutions require very

precise control, and very tight tolerances in manufacturing which are not feasible with

the available budget and resources.

With these limitations, the objective of the project is to develop a fully functional

device that can accurately and repeatedly pick tomatoes. The final device will be a

mobile robot, designed for outdoor use, that can identify tomatoes using machine vision,

and autonomously pick them using a robotic manipulator.

Objectives

Fast Response Speed

Smaller sized fruit such as tomatoes can be harvested much faster, less than 20

seconds each (an automatic tomato harvesting machine designed at Beijing University

of Technology achieved an operational time of 8 seconds [8]. Our robot aims to reduce

their completion times.

Easy and Intuitive to Operate

The machine should be simple to operate, requiring only minimal safety training.

Complex Terrains Functionable

The machine should be able to function on steep terrain with slopes exceeding 50°.

Many nurseries and farms, noticeably in China and India include steep terrain. Traditional

harvesters are limited to open fields with slopes under 30 [9]. The ability to operate on steep,

and uneven terrain would greatly improve the machines versatility.

Cost Efficient

The cost of the device should be minimized.

Integrable to Larger System

The machine should be integrable into a complete fruit harvesting process that also

includes fruit cleaning, grading, disinfection, artificial waxing etc.

Constraints

Multiple Degrees of Freedom Movement

At least four degrees of freedom of movement are required to allow for multiple

possible position configurations to avoid obstacles such as foliage.

Durable and Maintainable

Sensitive electronic components must be protected and made replaceable, most

mechanical components must be interchangeable and repairable. Many farms are in remote

areas and are not easily accessible by support technicians. Modern farm equipment is

dependent on electronics (which are often difficult or impossible to repair without a qualified

technician) which can cause delays in case of repairs.

Safe to Operate

The machine should meet Occupational Health and Safety Act (OHSA) standards, other

related regulations and local laws.

Safe for Greenery

The core advantage of an automatic harvester over mechanical harvesters such as lime

shakers, air blasters, and canopy shakers is that it does not damage the trees or fruits. To

preserve this fundamental advantage is imperative.

Weather and Dust Proof

The machine is expected to work outdoors under various conditions.

Fail Safe

The device must fail such that nearby workers are not injured.

Accurate Fruit Detection

The implemented fruit detection method should be able to identify fruit from a noisy

background, returning 3D coordinates to the processor. The fruit detection method should

work under various scenarios, including insufficient illuminance, strong light intensity (such as

at noon), movement, and partial occlusion.

Concept Generation and Selection

During the concept generation and selection process, a series of design techniques were

implemented, including functional decomposition, morphological analysis and the use of a decision

matrix. In this section, each generated concept will be explained, optimal solutions will be discussed,

and a comprehensive solution will be provided.

Functional decomposition

After analyzing the given constraints and objectives, to build a functional fruit-picking robot, the

following functions must be completed:

- Driving mechanism: The robot must move freely
- Picking mechanism: The robot must pick tomatoes
- Detaching mechanism: The robot must detach the tomatoes from their vine
- Collecting mechanism: The robot must store the collected tomatoes
- Machine vision: The robot must locate the tomatoes

Morphological Analysis

There are various ways to achieve above functions, after group brainstorming and

researching, multiple possible solutions for each subsystem were generated.

Moving Subsystem

1. Four wheels

This method is the simplest to implement, requiring four wheels that have high

coefficients of static friction to ensure the robot can travel over unpaved surfaces. The

advantage of this concept is that four wheels allow the robot to maneuver easily. The

disadvantage is the associated cost and it may not be able to operate on rough terrain.

2. Caterpillar tracks

Caterpillar tracks provide far more traction than wheels over unpaved surfaced.

Two motors are used to drive the tracks, with a large gear to provide torque, and a

pinion for tensioning.

3. Multi-Legged

A complex multi-legged walker can climb and travel over obstacles. Multiple

stepper motors, and complex linkages will be used to implement this mechanism,

adding significant complexity. The advantage is that it can travel easily on rough

surfaces, the disadvantage is its cost and complexity.

4. Rail

A railway system could be constructed on the ground for the robot to travel on.

This method is very simple but not cost-efficient. Although it is very easy to operate, a

railway system would have to be built throughout the operating environment, which is

very expensive. Additionally, the distance between the robot and the plant is fixed, so

the robot may be too far or too close to the plant to operate properly.

Picking Subsystem

To pick up an object in three-dimensional space, a robotic arm is the optimal solution

because it has six degrees of freedom. The following mechanisms will be implemented

on a robotic manipulator.

1. Clamp

The simplest possible solution, however, the stem needs to be cut to detach the

fruit from the plant. A detachment mechanism would be implemented. To facilitate force

control, a closed-loop control system is required for this mechanism to operate.

2. Small basket

This mechanism is a small basket with a detachment mechanism above. The

robot will detect the tomato, place the basket below it, then the detachment mechanism

cuts the stem. This method does not require a force control system.

3. Vacuum

Using a vacuum to collect the desired tomato can easily damage it. Furthermore,

it can be quite expensive, and complex to implement properly. This solution requires

significant power, which would result in high operating costs.

4. Transmission tube

This method of collecting the fruit is to cut the stem, then allow the fruit to fall

down a flexible rubber or PVC tube. This is the easiest, and most cost-effective way to

transport tomatoes.

Detaching Subsystem

1. Scissor

A pair of scissors will be attached to the picking mechanism to cut the stem

above the fruit.

2. Knife

A knife is connected to a stepper motor. After identifying the location of the stem,

the knife will pass through that location to cut the stem. However, the blade may

damage the plant.

3. Saw

A motor is connected to a saw blade. After identifying the location of the stem,

the saw will pass through that location to cut the stem. This method has the same

disadvantage as the knife, as it may damage the fruit.

Collection Subsystem

1. Basket
2. Case
3. Net

The previous three collection mechanisms are all considered as viable and

effective solutions.

Concept Selection

Go/No-Go Screening

Driving Subsystem

For the driving subsystem, the objectives that will be evaluated are:

Complexity: Difficulty to implement, test or operate

Maneuverability: Difficulty to change direction during operation

Cost: The value of money to manufacture

Safety: The level of danger inherent to operators

Durability: The ability to remain functional without excessive maintenance

or repair

Reliability: The capacity to perform as required over time

Table I: Movement Subsystem Go/ No-Go Matrix

| Complexity | Maneuverability | Cost | Safety | Durability | Reliability | Result
Four wheels | GO | GO | GO | GO | GO | GO | GO
Caterpillar bands | GO | GO | GO | GO | GO | GO | GO
Multi-Legged | NO-GO | GO | NO-GO | GO | GO | GO | NO-GO
Rail | GO | NO-GO | NO-GO | GO | GO | GO | NO-GO

Picking Subsystem

For the picking subsystem, the objectives that will be evaluated are as follows:

Complexity, Cost, Durability and Reliability: Same as above

Adaptability: Ability to pick different types or size of fruit

Safety to plants: The level of inherent danger to plants

Table II:Tomato Picking Subsystem Go/ No-Go Matrix

Complexity | Adaptability | Cost | Safety to
| | | plant
Durability | Reliability | Result

Clamp | GO | NO-GO | GO | NO-GO | GO | GO | NO-GO
Basket | GO | GO | GO | GO | GO | GO | GO
Vacuum | GO | GO | GO | GO | GO | GO | GO
tube | GO | GO | GO | GO | GO | GO | GO

Detaching Subsystem

For the detaching subsystem, the objective that will be evaluated is its safety

towards plants

Table III: Tomato Detachment Subsystem Go/ No-Go Matrix

| Safety to Plant | Result
Scissor | GO | GO
Knife | NO-GO | NO-GO
Saw | NO-GO | NO-GO

Collection Subsystem

All collecting methods are viable.

Decision Matrix

To select the optimal solution from the above generated concepts, a decision

matrix will be used. The decision matrix will be evaluated based on different criterial

corresponding weights will be assigned to each of the following:

Complexity (Weight=3): Difficulty to implement, test or operate

Cost (Weight=5): The value of money to produce

Efficiency (Weight=5): The ability to quickly achieve the desired result

Sustainability (Weight=3): The concept’s environmental impact

Durability (Weight=4): The ability to remain functional without excessive

maintenance or repair

Safety (Weight=4): The level of inherent danger to operators

Reliability (Weight=3): The capacity to perform as required over time

Adaptability (Weight=5): Ability to pick different types or size of fruit

Maneuverability (Weight=5): Difficulty to change direction during operation

Safety to plant (Weight=5): The level of inherent danger to plants

Table IV:Comprehensive Subsystem Decision Matrix Weight | Moving Subsystem

Picking; Subsystem; Detaching; Collecting; Four; Wheels; Caterpillar; Bands; Basket; Vacuum; Tube; Scissor; Case; Net; Complexity; Cost; Efficiency; Sustainability; Durability; Safety

Reliability; Adaptability; Maneuverability; Safety to plant; Total

Design Validation

Frame Analysis

The frame is made from extruded 1060 aluminum alloy beams, 1060 Aluminum

is a strong, lightweight material that suitable for various applications, in this application,

the frame will be supporting an approximate weight of 5 kg of fruit and 10 kg of robot

self-weight.

An FEA analysis was conducted with a loading scenario of 50N distributed force

on the base plate which simulates the approximate weight of 5kg, to ensure the

accuracy of the test, a fine mesh was used in this analysis with an element size of

8.62mm. The results of the FEA analysis are shown in the following figures.


Figure 4: FEA Analysis: Von Mises Stress

It was found that the maximum Von Mises stress occurs on the contact edge of

the plate and the frame, which is 1.131 MPa, the yield strength of H12 tempered 1060

aluminum is approximately 76 MPa, indicating no risk of failure by yielding.

Furthermore, 1060 aluminum is resistant to corrosion. [10]

The resultant displacement from the same analysis is shown below; it was found

that the maximum displacement of 0.015mm occurred along the center line of the plate.


Figure 5: FEA Analysis: Deflection

Motor Analysis

After measuring the weight of the empty robot to be 10kg, and by adding the payload

weight of 5kg, the loaded robot will have total weight of 15kg. A normal force of 36.75N can

be applied to each of the four wheels. Assuming the frictional coefficient between the rubber

wheels and a dry concert ground is 0.6, a frictional force of 22.05N must be overcome.

Based on Newton’s second law, a net force of 1.5N must be applied to allow the 15kg

device to accelerate at a rate of 0.1m
s

2

F = ma = (15kg) (

0.1m
s

2

) = 1.5N

Disregarding the moment of inertia of the wheel (as it was determined to be

inconsequential), the required torque for 0.1 m
s

2

.can be calculated as follows:

τ = F x r = (22.05N + 1.5N)x (0.09m) = 2.12 N. m

Equating the applied force and friction, the required steady-state torque can be

determined as follows.

τ = F x r = (22.05N)x (0.09m) = 1.98 N. m

By estimating the operational speed of 0.5 m
s

, the required rotational speed can

be calculated using the diameter of the wheel and the linear speed of the robot:

circ. = πd = 0.18m x π = 0.565m

f =

v
circ . =

0.5m
s
0.565m = 0.884 Hz

frpm = 60f = 60(0.884) = 53 rpm

Considering the limited budget, a brushed DC motor is the optimal solution.

In this application, a gearbox is required due to of the high speed, low torque output

from the motor.

Based on the specification that the selected motor must have a stall torque over 2.1

Nm and a rated torque ideally as close as possible to 2Nm to maximize mechanical

efficiency, a gearbox motor with the following properties was selected.

Voltage | No-load speed | Rated speed | Rated torque | No-load current | Rated current | Stall current
24V DC | 172±15 RPM | 122 ± 10 RPM | 2.5N.m | 0.3A | 2.3A | 7A

The motor has an integrated 1:51 gear reducer, which amplifies the rated torque

from 50mNm to 2.5Nm that will fulfill the design requirement. A CNC machined steel

shaft mount with an integrated bearing was also purchased to mount the motor on the

chassis. A 180mm diameter wheel with aluminum wheel hub and rubber tire will be

attached to the motor assembly. The motor can be controlled using pulse width

modulation. After a series of tests, a 15VDC supply, operating at a 30% duty cycle could

achieve the specified rate of 0.5m
s

. A peak speed of 1.7m
s

was observed during testing,

which would be implemented if not for safety considerations. For this device, rear

differential steering was used due to the potential for zero-turn-radius steering. After

completing the concept generation and selection phases of the design development,

construction began on both a physical prototype and a Solidworks assembly to model

the completed concept.

Image Processing Analysis

The image processing system has multiple stages of processing. The steps are

presented below:


First, the RGB channels are combined into grayscale. Since tomatoes are

saturated red with a mix of green, brown (red + green) and blue-sky background, a

linear algorithm that promotes red and demotes green and blue was used to create a

grayscale image.

Grayscale = 3 ∗ red channel − 2 ∗ (blue channel + green channel)


Figure 6: First Iteration Colour Segmentation

Complex lighting conditions often cause noises in the image and color

thresholding to create binary image is further exaggerating the problem. Therefore,

some techniques are used to remove these noises. As seen in Figure 6: First Iteration

Colour Segmentation the holes inside the tomatoes are from overexposure areas due to

the point light in the test environment. Filling the contour is required in later processing.

To get a cleaner image and fill the hole, morphological reconstruction is used on the

image to fill the small gaps and holes as shown in Figure 7: Tomato Segmentation with

Closed Contours.


Figure 7: Tomato Segmentation with Closed Contours

After removing overexposed spots, groups of pixel number fewer than 20 are

removed to solve the “salt and pepper” type of noise. After obtaining a cleaner image,

objects are separated by their pixel connectivity and unique numbers are assigned to

each pixel group to identify each tomato. The MATLAB image processing command

“bwlabel” is used to assign matrix numbers and to return the total number of objects.

To identify to the stem location, image objects are separated by their regions and

each region is individually processed to find the top location of that object. MATLAB’s

“find” command is used to return the top location (in the matrix) of each unique object.

Each location is determined based on its position relative to the surrounding area. The

relative location of selected pixel is compared to the location where the camera is

pointing at, the difference is used to command where the end effector should move to.

The process continues until there are no more identified tomatoes and their top pixels

are presented in the image. Using this procedure, all tomatoes can be identified and cut

in sequence.

This traditional image processing technique works well in relatively simple

environments. In later development of the actual product, it would be best to combine

traditional image processing with machine learning to work in more complex

environments. In this case, traditional image processing would be used to deblur or

remove noise, machine learning could act as a more robust method of identifing the

tomatoes.

Voice Recognition Analysis

The voice recognition system has three stages to process captured sound. The

first stage is to down sample the audio captured by the microphone. The second stage

is a bandpass filter to reduce surrounding noises. The third stage is TensorFlow based

machine learning to recognize the audio.

The microphone audio sampling rate is fixed 48khz, however the TensorFlow

model is trained on 16khz samples. As 48kHz is three times the 16kHz, to match the

16khz test signal, the recorded sample frequency is reduced by a factor of three.

A bandpass filter of 300Hz – 7kHz is implemented to reduce the surrounding

noises. It is found that pronunciation frequency of most western words lay in between

500Hz – 5000 Hz range. The goal of this voice recognition is to recognize a recorded

“Stop” sound. First a fast Fourier transformation is performed on the “Stop” sound to

analyze the harmonic spectrum.


This spectrogram shows that the “s” from “stop” has most energy around 7k Hz range,

the “top” sound has frequency expanding between 300 – 1k Hz range. Therefore, 300 –

7k Hz band filter is chosen. A Kaiser window FIR band pass filter is eventually

implemented. FIR is chosen over IIR because it’s much easier to preserve the linear

phase in FIR. Although some distortions in phase likely would not cause significant

problems using a machine learning model, FIR is still chosen to slightly increase model

accuracy. Because the voice recognition is running on a laptop in this prototype design,

an increased number of coefficients would not cause noticeably increased hardware

usage or scheduling issues. However, if the final product is relying on low end, low

power ARM chip to perform the tasks, IIR should be considered to reduce processing

power. Comparing between different window methods including Hamming, Gaussian,

and Chebyshev. Kaiser window is chosen as it offers a balance between a sharp

transient and the number of coefficients needed.

The TensorFlow based voice recognition is a retrained deep speech model using

customized training data instead of default training sets. The retrained model only

includes a very small set of known words, including “stop”, “start”, “left” and “right”.

Other words are fed into the unknown words category and trained as noise. This

retrained model with a much smaller number of words drastically increases recognition

success rate. The current software divides the audio stream to 1.3 second clip to feed

into the machine learning model. This length offers a balance between recognition

success rate and response time. An improvement could be made on caching strategy,

double buffering could be implemented so that audio would not be cut between two clips

and this would increase voice recognition rate.

Navigational System Analysis

The navigational system uses an 8-bit hall-effect magnetic line tracker and a 1.5-inch

magnetic strip. The magnetic tape is to be adhered to ground and line tracking sensor

detects the horizontal relative location of the tape. By reading the location information into a

microprocessor and using if-then logic, the speed of the two motor can be effectively

controlled.

The magnetic sensor communicates serially based on a MODBUS-RTU

communication protocol or by outputting the states of each of the hall-effect sensors NPN

open-drain configurations. Tracking was achieved by polling each of the sensors

independently. Using the internal pull-up resistors in the microprocessor, this information

can be read directly through corresponding digital pins. After processing, the

microprocessor outputs a 5V PWM signal, which is amplified to a nominal voltage using an

integrated motor driver.

Manipulator Analysis

The manipulator implemented in the design and prototype uses open-loop

control, as the lack of feedback sensors was regrettably not discovered until after assembly and initial testing. This resulted in minor observable steady-state error in the

z-direction, which was mitigated using a constant offset. The manipulator appeared to

have some sort of integrated control as it traversed its range of motion in under one

second without overshoot, however the joint position data was not accessible to the

programmer. The manipulator has a reachable workspace consisting of a 36cm dome

centered at a height of 9cm above its attached platform.

Forward Kinematics

To model the manipulator, both forward and inverse kinematic models were generated.

The forward kinematics were determined based on the following DH parameters, from

which a series of transformation matrices were calculated for each of the joint

locations. The theta values used were adjusted such that the

commanded angles inherently programmed into the controller matched the measured

joint angles observed. Based on the following parameters an accurate model of the

manipulator kinematics was generated using MATLAB.

Table V: HIWONDER Manipulator: DH Parameters

I | αi-1 | ai-1 | di | Θi
1 | 0 | 0 | 0.09 | Θ1 – π/2
2 | 0 | 0 | 0 | Θ2 – π/2
3 | -π/2 | 0.11 | 0 | Θ3
4 | 0 | 0.09 | 0 | Θ4
5 | 0 | 0.16 | 0 | 0

Inverse Kinematics

The inverse kinematics of the manipulator were determined using an iterative

algorithm called FABRIK, Forward and Backwards Reaching Inverse

Kinematics developed at the Department of Engineering at Cambridge University,

Cambridge, UK [11]. The algorithm is best demonstrated in the following Figure 8 . This

method is far simpler than others used as it does not require matrix manipulation,

instead using simple geometry. This algorithm operates by positioning the end-effector

at the desired position Figure 8 (b) , drawing a line between that position and the next

joint n-1, positioning joint n-1 a distance equal to the length of the link away from joint n

along that line Figure 8(c), and repeating for the remaining joints Figure 8 (d). Then, the

base joint is placed at its proper location Figure 8 (e). The same process

repeats propagating outwards from the base towards the end effector. This cycle

repeats until the base is located at its appropriate location and the end-effector is close

enough to its desired position to be considered acceptable Figure 8 (f). Testing in

MATLAB resulted in the end-effector being located within 0.1mm from the desired

position, although higher accuracy would be possible with more iterations.

This algorithm works very well in solving planar manipulators; however, a slight

modification was required to allow the algorithm to accurately model the manipulator

used which is a planar manipulator with a rotating base. Using the coordinate

frame of the base rather than the universal frame in this analysis resolved this issue.

Figure 8: FABRIK Algorithm


The resolution of the manipulator is less precise than can allow for the

0.1mm accuracy determined by the FABRIK algorithm. Each joint has a resolution of

0.18⁰, which, during testing corresponded to an accuracy of ±0.5 cm in the x and y

directions. This is also due to inherent error in the controller provided, which does not

appear to account for the weight of the manipulator based on the observed steady state

error in the z direction.

Design Refinement

Motor Refinement

After completing the CAD model of the chassis and manipulator, it was found that

the weight of the device previously estimated to be 7 kg was inaccurate. The completed

model, created from 1060 aluminum, had a mass of 10kg. After adding the weight of fruit of 5kg, the fully-loaded robot will have a weight of 15kg. At this stage, the original

gearbox motor selected was replaced with a different model which integrated a 51X

reduction. This allowed the device to operate closer to its rated torque, improving its

efficiency and the devices battery life. The physical dimensions of the motor were the

same, as was the housing used in both models. No other modifications to the chassis

construction were needed.

The motor specifications of two iterations can be found as follows:

Table VI: Drive Motor Selection Iteration

Gear Ratio | Voltage | No-load speed | Rated speed | Rated torque | No-load current | Rated current | Stall current
1:27 | 24V DC | 325±30 RPM | 230 ± 20 RPM | 1.324N.m | 0.3A | 2.3A | 7A
1:51 | 24V DC | 172±15 RPM | 122 ± 10 RPM | 2.5N.m | 0.3A | 2.3A | 7A

Storage Refinement

After the construction of collection subsystem, it was found that there was no

effective way to retrieve the fruit as there is no openable door to release the container.

The refinement made will be to construct an openable door at the other side that is

opposite to the transmission tube entrance. To achieve full automation, a servo will be

connected to the door which will open at a designated location when the robot detects

the container is full. This can be done by using a pressure sensor placed at the bottom

of container.

Manipulator Refinement

Based on the testing done, and the prototype construction, there are several key

refinements that need to be made between the prototype and the final design. The first

refinement is to install feedback sensors into the manipulator or to use a manipulator

from a different manufacturer that allows for closed-loop control. In the case of the

prototype, the accuracy of the manipulator was greatly improved by implementing a

constant offset to the commanded position to the shoulder servo, however implementing

feedback sensors would have greatly improved the design.

The end-effector was modified into a cutting mechanism that isolates and

separates the tomato from its vine. This mechanism was iterated multiple times

beginning as a simple claw-style gripper as was originally installed on the manipulator.

The claw was modified into a scissor cutter by attaching blades to each of the grippers,

due to the lack of precise control possible with the open loop control of the manipulator,

this design would cause undue damage to the vine and surrounding tomatoes. Finally,

the isolation cutter was developed that would encompass the tomato and cut both

above and in front of the tomato simultaneously. Unfortunately, this design was not able

to be fabricated due to the closure of university facilities. The scissor cutter was

implemented, tested, and proven to be an effective cutting instrument; however, it lacks

the safeguards of the isolation cutter.

Prototype Development

The prototype is developed to be 1:1 and fully functional, the prototype

constitutes of serval subsystems including a driving subsystem, picking subsystem,

collection subsystem, recognition subsystem and detachment subsystem.

Driving Subsystem

The driving subsystem is composed of two driving wheels that are mounted to

DC motors, two driven wheels and an 8-bit magnetic line tracker. The line tracker will

read the relative horizontal location of the magnetic strip on the ground and outputs this

to a microprocessor. The microprocessor will differentiate the speed of two motors

based on given information. Two 5V PWM signals are generated based on the turning

scenario. The motor driver amplifies the 5V signal to 15V and sends it to each of the

motors.

Collection Subsystem

The collection subsystem is integrated within the frame’s built-in 300mm x

300mm x 100mm space beneath the manipulator. Three of the side panels and the

base panel were fabricated from 2.5mm acrylic. The final side panel, which contained

the connection interface with the transmission tube was fabricated from ½ inch plywood

as the acrylic panel originally to be used was found to be too brittle to withstand the use

of a 4-inch hole saw. If the panel was to be fabricated using a laser cutter, the original

acrylic panel could have been used, however that service was unavailable due to the

closure of university facilities. A flexible plastic tube (dryer duct) was inserted into the

hole in the collection bin and connected to the manipulator end-effector using cable-ties.

Detaching & Picking Subsystem

To detach the tomato from the vine, the original end effector was modified by

adding two razer blades. Thich mechanism operates similarly to garden pruners. The

tomato then falls down a flexible plastic tube into the collection bin.


Figure 9: Manually Actuated Detachment Mechanism

Recognition Subsystem

The recognition subsystem uses a webcam as its the input device, the captured

image is processed by MATLAB at a resolution of 640x460 to reduce processing time.

The capture framerate is set to 10 frames per second for this application. Various image

processing techniques were used including noise removal, RGB to binary conversion,

template matching and morphological reconstruction.

Prototype Testing and Evaluation

After constructing the prototype, each of the core functions of the device were

tested independently before being integrated into a single system. However, due to a

lack of access to university facilities, the final system integration was unable to be

completed as required connecting and mounting components could not be fabricated.

What follows summarizes the tests that were completed, before and after iterations

were made.

Linear Speed Test

In this test the device was fully constructed, and the linear speed of the device

was measured. Between trials the average voltage applied across the driving motors

was modified. The speed of the device was measured, and the battery life was

estimated. The purpose of this test was to determine the performance capabilities of the

device as could be directly related to its viability as an effective supplement to tomato

harvesting workers. Assuming the steady-state torque applied by the motor remained

consistent, the battery life at each speed was estimated as a result.

Table VII: Linear Speed Recorded Test Data

Vnom (V) | Duty Cycle | Vavg (V) | Speed (m/s)
15 | 30% | 4.5 | 0.50
24 | 30% | 7.2 | 0.80
10 | 80% | 8 | 0.85
15 | 60% | 9 | 1.00
15 | 100% | 15 | 1.67

Observed Speed (m/s); Average Voltage (V); Steady-State Linear Speed Test

Figure 10: Steady-State Linear Speed Test Data Plotted with Linear Regression

Based on the speed data observed, the average current (which was not

recorded) could be estimated along with the estimated power consumption and battery

life.

Table VIII: Power Analysis and Estimated Battery Life using a 5 Ah Battery

Vavg (V) | Speed (m/s) | Speed (rad/s) | Torque (Nm) | Power (W) | Iavg (A) | 5 Ah Battery Life (estimated)
3 | 0.30 | 3.34 | 1.98 | 6.61 | 2.20 | 2.27
4.5 | 0.50 | 5.56 | 1.98 | 11.01 | 2.44 | 2.05
7.2 | 0.80 | 8.90 | 1.98 | 17.62 | 2.45 | 2.04
8 | 0.85 | 9.45 | 1.98 | 18.71 | 2.34 | 2.14
9 | 1.00 | 11.12 | 1.98 | 22.02 | 2.45 | 2.04
15 | 1.67 | 18.57 | 1.98 | 36.77 | 2.45 | 2.04

Turning Speed Test

As centripetal force limits the maximum speed the device can achieve while

turning, it was necessary to determine the highest possible speed the device could turn

while tracking a 3 cm wide magnetic track. To conduct this test approximately 2m of

magnetic track was fixed to the floor with a radium of curvature of approximately 1m.

The robot was placed at the end of the track and its speed was gradually increased until

the device was no longer able to follow the track. This radius of curvature was selected

to represent the device reaching the end of an aisle of plants and turning to travel in the

opposite direction along an adjacent aisle. Each trial was simply graded as pass/fail

depending on if the robot could successfully track the magnetic strip.

Table IX: Turning Speed Test

Speed (m/s) | Pass / fail
0.30 | Pass
0.50 | Pass
0.80 | Pass
0.85 | Pass
1.00 | Fail
1.67 | Fail

Based on the results of the prior two tests, the device could successfully operate

at a peak linear speed of 1.67 m/s and a peak turning speed of 0.8 m/s. This distinction

was implemented in the navigation code to maximize the efficiency of the device

Manipulator Inverse Kinematics Testing

In the following two tests, a series of positions are commanded to the

manipulator. It was during this stage of testing that it was discovered that the

manipulator purchased had no feedback devices in its servos, indicating that only open-

loop control was possible. This resulted in a lack of accuracy in the vertical z-direction

as the device was not capable of compensating for its own weight.

Table X: Manipulator Accuracy Test Pre-calibration

Commanded Position (X, Y, Z)Actual Position (X, Y, Z)

25 | 20 | 20 | 25 | 20 | 5
20 | 20 | 20 | 20 | 20 | 15
10 | 20 | 20 | 10 | 20 | 20
-10 | 20 | 20 | -10 | 20 | 20
-20 | 20 | 20 | -20 | 20 | 15
-25 | 20 | 20 | -25 | 20 | 5
0 | 0 | 45 | 0 | 5 | 40
0 | 10 | 30 | 0 | 12 | 25
0 | 15 | 30 | 0 | 15 | 25
0 | 20 | 30 | 0 | 20 | 25
0 | 25 | 30 | 0 | 25 | 30
0 | 30 | 30 | 0 | 30 | 20
0 | 35 | 15 | 0 | 35 | 10

Fortunately, this error could effectively be mitigated by adding a 10-degree offset

to the shoulder motor. This had eliminated the effect of the observed discrepancy while

also reducing the radial play of the motor in question.

Table XI: Manipulator Accuracy Test: Post-calibration

Commanded Position (X, Y, Z)Actual Position (X, Y, Z)

25 | 20 | 20 | 25 | 20 | 18
20 | 20 | 20 | 20 | 20 | 20
10 | 20 | 20 | 10 | 20 | 22
-10 | 20 | 20 | -10 | 20 | 22
-20 | 20 | 20 | -20 | 20 | 20
-25 | 20 | 20 | -25 | 20 | 18
0 | 0 | 45 | 0 | 0 | 45
0 | 10 | 30 | 0 | 10 | 32
0 | 15 | 30 | 0 | 15 | 32
0 | 20 | 30 | 0 | 20 | 30
0 | 25 | 30 | 0 | 25 | 28
0 | 30 | 30 | 0 | 30 | 28
0 | 35 | 15 | 0 | 35 | 15

Due to the poor design of the purchased manipulator, the elbow servo

overheated and ultimately burned out on two different units. This was under normal

operating conditions. As a result, the reachable workspace was greatly reduced as the

manipulator lost a degree of freedom. The revised DH parameters are as follows as the

servo became locked in a colinear configuration with the following link.

Table XII: Revised DH Parameters After Motor Failure

I | αi-1 | ai-1 | di | Θi
1 | 0 | 0 | 0.09 Θ1 – π/2
2 | 0 | 0 | 0 | Θ2 – π/2
3 -π/2 0.11 | | | 0 | 0
4 | 0 | 0.09 | 0 | Θ4
5 | 0 | 0.16 | 0 | 0

Prototype Modification and Improvements

Chassis Modifications

The original prototype was designed to test the functionality of the driving

mechanism and to aid the design of the original gearbox design. Specifically, it was

designed to configure the layout of the gears, shafts, bearings and other components

with the integrated storage compartment and power supply. The prototype was not

configurable as its replacement was, however, it was fully enclosed, waterproof, and

served as an initial concept or starting point from which iterations could be made. This

chassis was within budget costing approximately $40; however, it was difficult to

develop further as it was constructed from acrylic.

The second and final chassis was constructed from extruded aluminum beams

and cast aluminum brackets. This chassis cost approximately $115 to fabricate. The

revised chassis was very configurable and simple to test as it was assembled with

machine screws and aluminum brackets.

Line Tracker Modifications

In the original design and prototype, optical encoders were to be used as

feedback devices for the navigation system. The rationale for this decision being their

resistance to their environment, specifically their indifference to the cleanliness of the

floor. However, it was suggested that this concept be modified to an external navigation

system as an encoder would not be able to distinguish if a wheel was spinning freely

without linear movement. This prompted the switch to a magnetic line tracking system

as was implemented.

The use of individual hall-effect sensors, while proving cost-efficient was

ineffective primarily due to how close they could be physically installed relative to each

other (approximately 3cm apart) and their interference with each other after removing

their housings to reduce this distance. The integrated magnetic line tracking sensor was

used as a result

Manipulator Modifications

Based on the testing done with the manipulator, it quickly became apparent that

is was only capable of open-loop control as no feedback devices were installed into any

of the servos use in its construction. As a result, the observed error in the vertical

direction resulting from the devices own weight could not be eliminated through closed-

loop control schemes such as PID controllers. Instead, a constant offset was applied to

the commanded position of the shoulder motor to counteract the radial play and steady-

state error observed in prior testing. The value of this offset was iteratively modified to

ensure the repeatability of the end-effector location followed a normal distribution

centered about the desired position in that direction. The planar position (x/y) was

consistently accurate and repeatable.

Power Electronic Modifications

Nearing the completion of the prototype construction, the two battery packs

originally used were to be combined into a single pack with 15V and 7.5V supplies

being separated using a simple breadboard voltage divider. This simple change was

made to reduce the cost of the device and to simplify maintenance for the operator.

Image Processing Modifications

The algorithm used to identify and segment the tomatoes from the background

was iteratively developed. The initial testing gave simple grayscale photos, in which the

red colour was identified and highlighted. The second iteration was to create closed

objects to account for oversaturation resulting from intense light. Next, the objects are

identified independently and isolated as unique objects; at this stage the location of the

object can referenced by the manipulator. The edges and top of the object can be

determined and were intended to be used by the isolation cutter mechanism, which

unfortunately was never fabricated due to the lack of access to university facilities.


Overall, the image processing software | was

completed except the depth sensing (z-axis) part which works with ultrasonic sensor to

control the manipulator’s movement towards to away from the identified tomatoes. At

the current stage, the image processing software can move manipulator in x-axis and y-

axis (left, right, up and down), but unable to move in z-axis (towards, away) to actually

perform the task.

Figure 11: Object Isolation Test Setup Figure 12: Object Isolation: Computer Vision Results

Justification for Limited Prototype Functionality

The primary shortcoming in the prototype functionality was in the implementation

of the cutting mechanism. After the design of the cutting mechanism was postponed

due to a focus on the chassis and manipulator inverse kinematics, the ultimate

fabrication of the mechanism was unfortunately not completed. This was ultimately a

result of the lack of access to university facilities in the final weeks of the project in

which the cutting mechanism, hose attachment fixture, and collection bin were to be

fabricated. To fabricate these components, two pieces of equipment were required: the

band saw to accurately cut acrylic, and a sheet-metal brake to create the attachment

fixture. For the purposes of testing the cutting ability of the manipulator, two blades were

attached to the included claw manipulator using zip ties to demonstrate the claw motor

was strong enough to cut through material.

The ultrasonic sensor is not installed on the manipulator end-effector to work with

the image processing software. The incomplete of ultrasonic sensor is because of two

reasons: 1. The manipulator cannot support the weight of the additional ultrasonic

device 2. Support structure was not fabricated to properly attach and install the

ultrasonic on the end-effector. The absence of ultrasonic sensor results in image

processing unable to command the manipulator to move in z-axis (depth).

During testing, it was discovered that the manipulator was poorly designed and

that servo 3, the “elbow” servo, was underspecified. On two separate units this same

servo burned out. Rather than disassemble, return, and reassemble a new manipulator,

the same manipulator was continually used for testing with a reduced range of motion.

This was to save both time and money during development. The reduction in the range of motion predominantly effected the manipulators ability to reach a cylindrical area

above its own base, it also prevented the manipulator from reaching below its base.

This was accommodated for during testing when selecting commanded positions,

although the workspace reduction is significant.

Resources and Budget

The following table outlines a comprehensive, itemized invoice of the material

costs associated with the construction of the prototype and ultimately the final design of

the fruit picking robot.

Table XIII: Itemized Prototype Fabrication Cost

Item | Quantity | Unit Cost | Total Cost
Drive wheel | 2 | $18.63 | $37.26
Driven wheel | 2 | $12.61 | $25.22
8-Bit magnetic line tracking sensor | 1 | $55.51 | $55.51
BTN7971 motor driver | 1 | $24.09 | $24.09
MD36 35W 24V DC Motor with optical encoder | 2 | $73.92 | $147.84
Ultrasonic sensor | 1 | $1.32 | $1.32
24V to 5V voltage converter | 1 | $3.20 | $3.20
M5 washer | 50 | $0.02 | $1.00
M5-12 screw | 10 | $0.08 | $0.80
M5-14 screw | 10 | $0.09 | $0.90
M5 – 16 screw | 10 | $0.09 | $0.90

M5 nylon lock nut | 30 | $0.04 | $1.20
Aluminum beam corner bracket | 40 | $0.53 | $21.20
80cm 2020 aluminum beam | 10 | $1.67 | $16.70
5-DOF Manipulator and associated hardware | 1 | $165.29 | $165.29
Acrylic Panels | 4 | $1.10 | $4.40
100 mm flexible hose | 1 | $2.50 | $2.50
| | Total | $509.89

Potential Cost Savings

Table XIV: Potential Cost Savings

Item | Cost | Savings
Reed sensor SPST | $18.00 | $37.51
24V 5300RPM DC motor | $25.84 | $96.15
Injection molded wheels | $10 | $24.25
Total Savings | | $156.11
Potential cost | | $353.78

As can be seen, the project did exceed the budget by $210, this could be

addressed by using single hall-effect sensors instead of the integrated sensor, using a

12V motor instead of the 24V motor specified and operating at a lower efficiency

(sacrificing battery life), and at a higher average current. Savings also could have been

had on the driving wheels. The wheel specified are cast aluminum, plastic wheels could

have been used at the expense of durability.

Conclusions

Since the last deliverable, substantial progress had been made alongside the

greatest challenges of the term as a result of the COVID-19 pandemic. The

development of each of the independent subsystems was completed, although they

were not fully integrated together. The final cutting mechanism, the ultrasonic mount

that would allow the image processing system to achieve depth perception, nor the

collection bin were fully fabricated due to a lack of access of machinery and laser

cutting services.

The image processing system can successfully identify and isolate tomatoes,

even if they are partially in occluded by each other, also, the edges of the tomatoes can

be identified indicating the appropriate position of the isolation cutter. The manipulator

was discovered to not include any feedback sensors to allow for closed loop control,

and the elbow motor burnt out twice during testing. Considering this, it can accurately

move to a commanded cartesian coordinate location, despite having a limited reachable

workspace due to the motor failure on the prototype. The magnetic line tracking

navigation system works perfectly across multiple surfaces. Given the opportunity, the

missing components would be fabricated, and the independent subsystems would be

integrated. In addition, more extensive testing would be done including testing on live

tomato plants instead of greenhouse tomatoes, and perhaps the manipulator would

have been replaced (the one selected had no datasheet or specifications provided) with

a different, higher quality manipulator.

References

[1] Canadian Agricultural Human Resources Council, "Argiculture 2025: How the

Sector's Labour Challenges Will Shape Its Future," Canadian Agricultural Human

Resource Council, Ottawa, 2016.

[2] Canadian Agricultural Human Resources Council, "How Labour Challanges Will

Shape the Future of Agriculture: Agricultural Forcast to 2029," Canadian

Agricultural Human Resources Council, Ottawa, 2019.

[3] T. Sasaki, K. Iwasaki and I. Mori, "Overtime, Job Stressors, Sleep/Rest, and

Fatigue of Japanese Workers in a Company," Industrial Health, 2007.

[4] A. Shikdar and Das, Biman, "The relationship between worker satisfaction and

productivity in a repetitive industrial task," Applied Ergonomics, 2003.

[5] G. Kaskooli, Interviewee, Farmworker vs Robot. [Interview]. 17 February 2019.
[6] M. Frost, "Express," Express Newspaper, 11 October 2019. [Online]. Available:

https://www.express.co.uk/finance/city/1189306/raspberry-picking-robot-fruit-veg-

harvesting. [Accessed 2 Novemeber 2019].

[7] M. Dosser, H. Bischof and M. Wiltsche, "Color Blob Segmentation by MSER

Analysis," in 2006 International Conference on Image Processing, Atlanta, GA,

USA, 2006 .

[8] L. L. Wang, B. Zhao, J. W. Fan, X. A. Hu, S. Wei, Y. S. Li, Q. B. Zhou and C. Wei,

"Development of a tomato harvesting robot used in greenhouse," International

Journal of Agricultural and Biological Engineering, vol. 10, no. 4, pp. 140-149,

2016.

[9] H. Heinimann, "Ground-Based Harvesting Technologies for Steep Slopes," Proc.

Int. Mountain Logging and 10th Pacific Northwest Skyline Symposium, 1999.

[10] ASM Internation, "Properties of Wrought Aluminum and Aluminum Alloys," in ASM

Handbook, Voltume 2: Properties and Selection: Nonferrous Alloys and Special

Purpose Materials, ASM Handbook Committee, 1990, pp. 62-63.

[11] A. Arisidou and J. Lasenby, "FABRIK: A fast, iterative solver for the Inverse

Kinematics problem," Graphical Models, vol. 73, no. 5, pp. 243-260, 2011.

[12] S. Hayashi, K. Ganno, Y. Ishii and I. Tanaka, "Robotic Harvesting System for

Eggplants," Japan Agricultural Research Quarterly, pp. 163-168, June 2002.

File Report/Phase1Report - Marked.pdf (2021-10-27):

Fruit Picking Robot: Phase 1 Report

Coordinator: Prof. Samani

Faculty Advisor: Prof. Brown

University of Western Ontario

MSE 4499: Mechatronics Capstone Design Project

Team Members

### Alexander Cleator: 250 834 890

### Qi Qi: 250 916 060

### Ziqin Shang: 250 890 594

### Mingyang Xu: 250 902 744

## Contents

## Executive Summary

The purpose of this report is to fully communicate the work done on an autonomous fruit picking mobile robot. The agricultural industry is currently experiencing a significant labour shortage that is only projected to grow with the coming years, resulting in an estimated monetary loss of $2.9 billion in 2017. The development of this device is to act as a pilot project regarding the automation of the harvesting of soft fruit as a means of offsetting this loss. The completion of a fruit picking robot is divided into several subtasks including a driving system, a fruit detachment system, a machine vision system, and a collection method, which combined will yield a functional device. Currently, several robots in development can complete this same task, however they are astronomically expensive, beyond the financial reach of most farm owner/operators. The concept of design a four-wheel driven robot, with an attached robotic manipulator, and a collection base is fully justified, along with the functional decomposition, morphological analysis, and decision matrix that led to its inception. The concept itself is detailed, and validation work is completed, with proof that the selected gearbox reduction will have an operating life exceeding 10,000 hours. A Solidworks model of the entire concept is produced, along with a simplified model better suited for analysis indicating the mass of the robotic manipulator will cause a deflection in the chassis top panel of less than 1mm. Fatigue analysis is completed on both the gears and shafts to be used in the driving system, finalizing a completed first iteration of this subsystem, and development of the machine vision system to be used is communicated and justified. Finally, an updated budget and schedule is proposed based the current work done, and the remaining work to be done is rescheduled to ensure the project is completed.
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

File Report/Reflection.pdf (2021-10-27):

# Reflections and Lessons Learned

# MSE 4499

## Ziqin Shang 250890594

## Apr 10th, 2020

## Problem analysis & Design

At the beginning of the course, I had limited amount of experience in design and develop an entire robot, I

had experience in working on mechanical component, but for other aspects such as electronics and software,

I have a little prior experience from second year design project, so this project challenged me to work with

electronics and write corresponding code.

For the development of drive system, firstly I calculated the required torque and speed for the motor, then
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

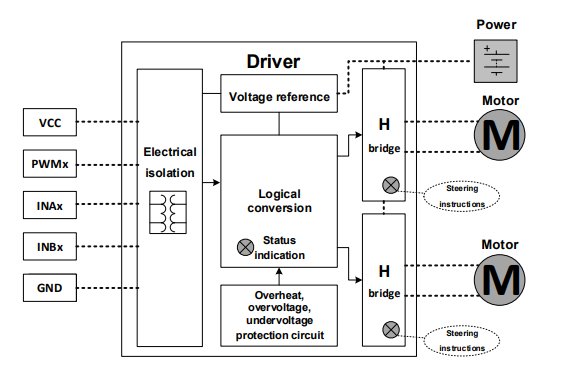
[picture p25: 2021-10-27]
CAD/motor driver schematic.png

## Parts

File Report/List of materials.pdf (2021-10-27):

# List of materials

Drive wheel 180mm X2 ¥198

Driven wheel 73.5mm X2 ¥134

Magnetic tape sensor 8-bit X1 ¥294.87

Magnetic tape X2 ¥10.4

8mm FlangeX2 ¥24.87

BTN7971 Dual DC motor drive module X1 ¥128

MD36 35w DC motor with optical encoder, 230rpm, 1.35N.m, 24V X2 ¥892

HC-SR04 Ultrasonic sensor X2 ¥13.8

Ultrasonic sensor holder X2 ¥5.8

Voltage stabilization module 24V to 5V X2 ¥33.6

M5 washer X50 ¥5

M5*12 screw X10 ¥4.2

M5*14 screw X10 ¥4.5

M5*16 screw X10 ¥4.5

M5 tight nut X30 ¥6

Aluminum beam fastener X40 ¥112

Aluminum beam 80cm X10 ¥88.5

Total ¥1960.04 = $369.75

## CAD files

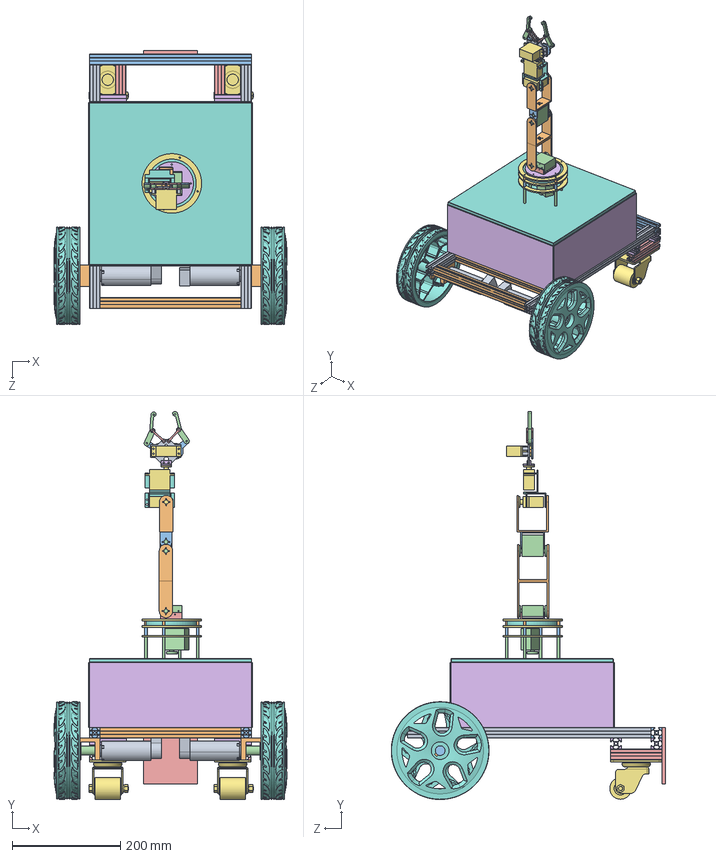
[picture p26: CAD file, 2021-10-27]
CAD/Robot Final version.SLDASM
430.2 x 717.3 x 507.4 mm
2020 alu section 450mm x 2
2020 alu section 260mm x 5
2020 alu section362.78mm x 3
2020 alu section 100mm x 4
2020 alu section 95mm x 4
2020 alu section 69mm x 4
JQR03210-40ALCPU612 x 2
180mm wheel x 2
DCmotor x 2
motorholder x 2
wheelshaftconnector x 2
motorshaft x 2
magneticsensorholder
container wall x 3
container base plate
manipulatorbase
gripper base plate
spacer x 3
drive gear x 2
gripper x 4
link x 4
gripper mount x 2
LFD-O6 Servo x 3
servo mount x 2
bearing
large U bracket x 3
small U bracket
LDX-218 Digital Servo x 3
base LDX-218 Servo Mount
upper base plate
base ring x 3
large bearing
lower base plate
9mm column x 4
15mm column x 4
40 mm column x 4
container wall with hole

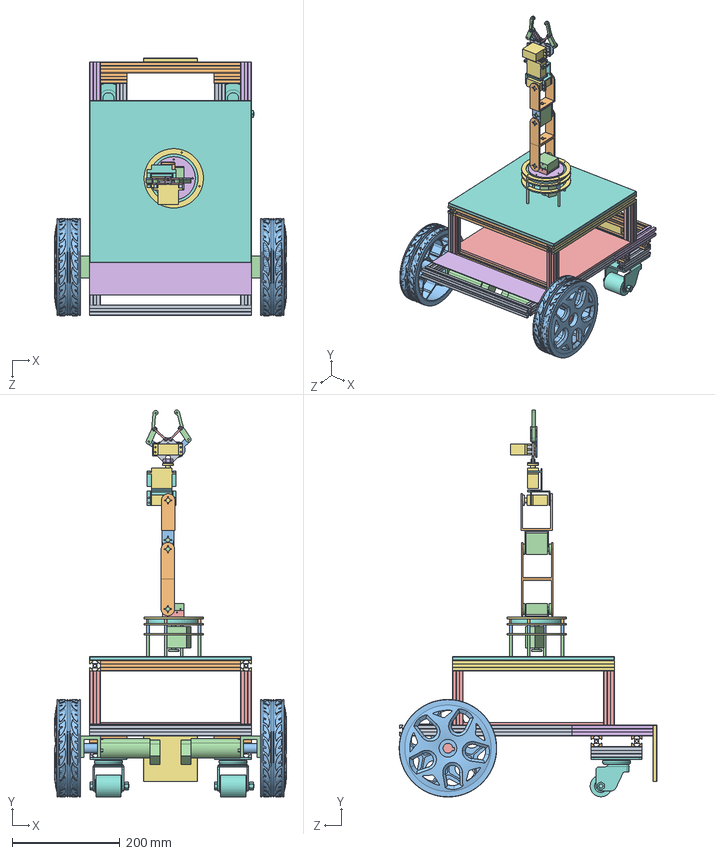
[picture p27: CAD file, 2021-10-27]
CAD/Frame.SLDASM
430.2 x 717.2 x 477.4 mm
2020 alu section x 3
2020 alu section 260mm x 6
180mm wheel x 2
DCmotor x 2
2020 alu section 100mm x 4
2020 alu section150mm x 2
2020 alu section362.78mm x 2
JQR03210-40ALCPU612 x 2
2020 alu section 95mm x 4
2020 alu section 69mm x 4
motorshaft x 2
motorholder x 2
wheelshaftconnector x 2
circuit board holder
magneticsensorholder
manipulatorbase
gripper base plate
spacer x 3
drive gear x 2
gripper x 4
link x 4
gripper mount x 2
LFD-O6 Servo x 3
servo mount x 2
bearing
large U bracket x 3
small U bracket
LDX-218 Digital Servo x 3
base LDX-218 Servo Mount
upper base plate
base ring x 3
large bearing
lower base plate
9mm column x 4
15mm column x 4
40 mm column x 4
container base plate

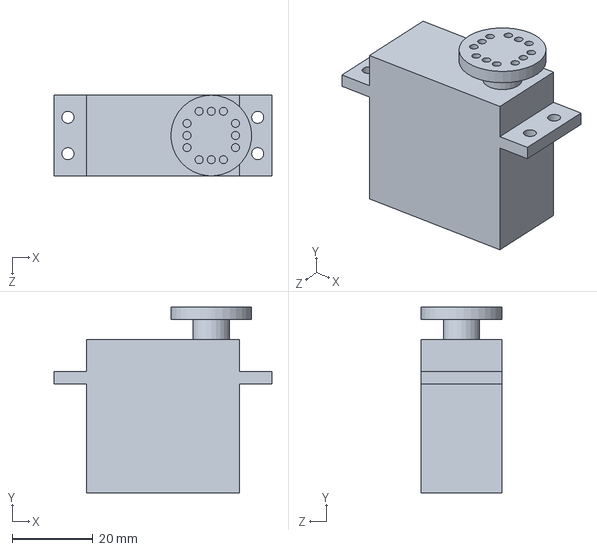
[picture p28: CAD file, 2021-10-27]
CAD/manipulator/LFD-O6 Servo.SLDPRT
54.0 x 46.0 x 20.0 mm

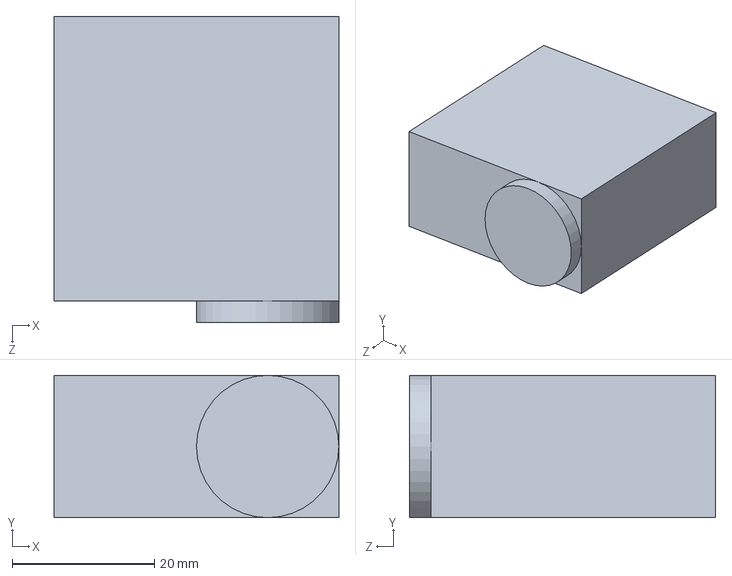
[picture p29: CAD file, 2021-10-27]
CAD/motor.SLDPRT
40.0 x 20.0 x 43.0 mm

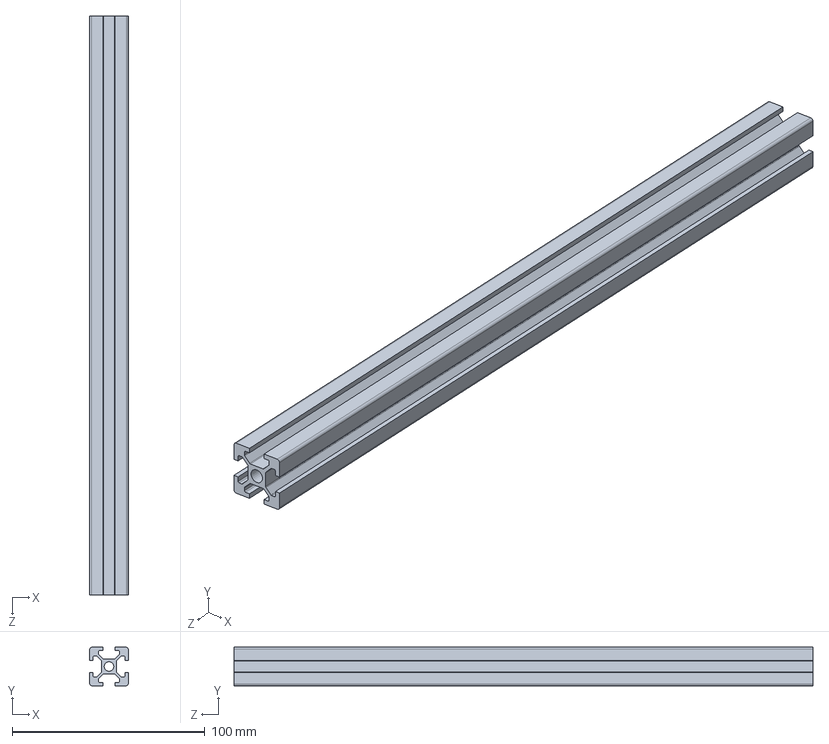
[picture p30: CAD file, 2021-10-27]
CAD/2020 alu section362.78mm.SLDPRT
20.0 x 20.0 x 300.0 mm

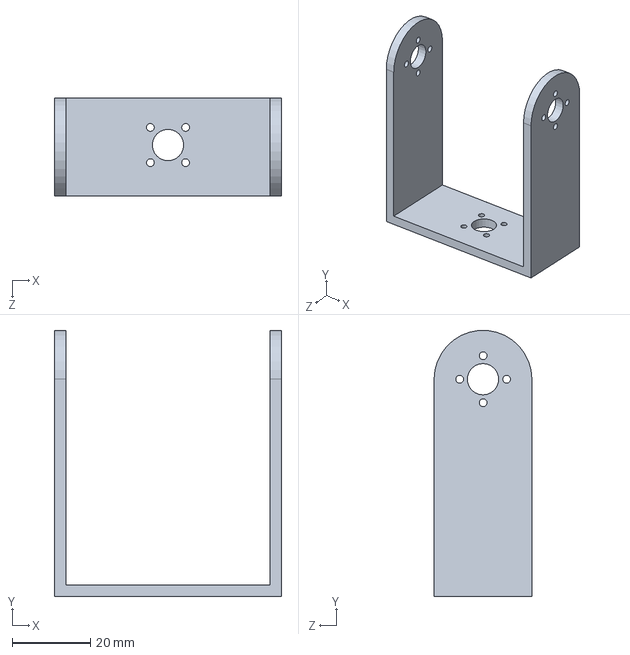
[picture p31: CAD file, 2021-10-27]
CAD/manipulator/large U bracket.SLDPRT
58.0 x 67.9 x 25.0 mm

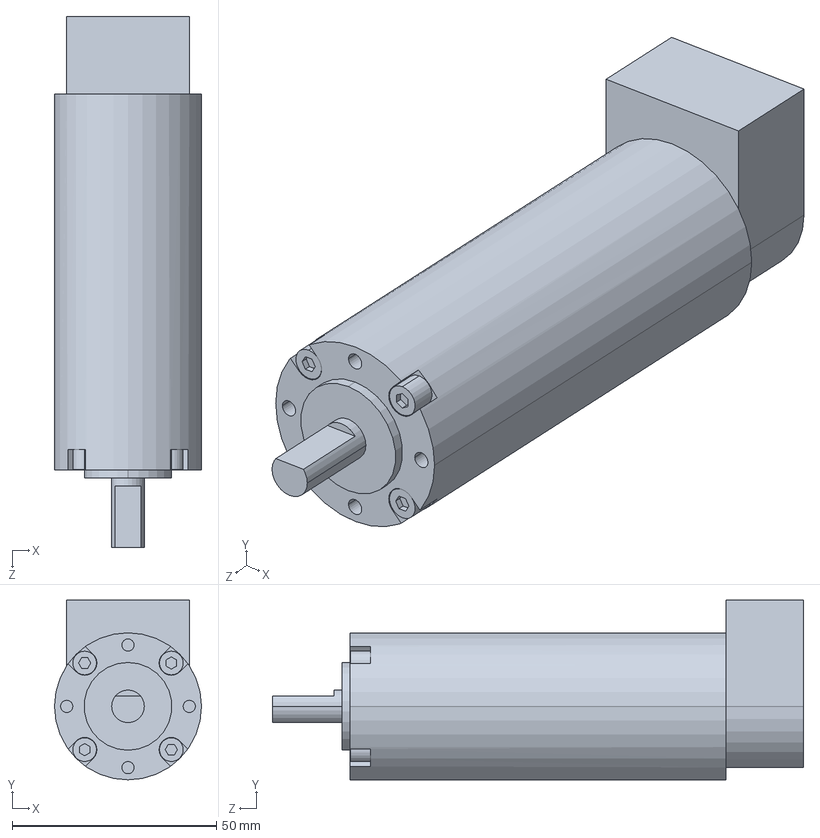
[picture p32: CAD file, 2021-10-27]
CAD/DCmotor.SLDPRT
36.0 x 44.0 x 130.0 mm

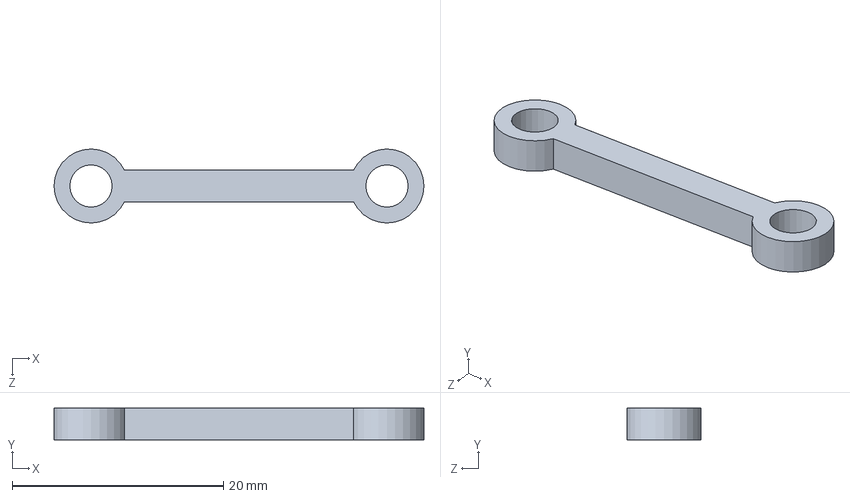
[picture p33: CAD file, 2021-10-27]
CAD/manipulator/link.SLDPRT
35.0 x 3.00 x 7.00 mm

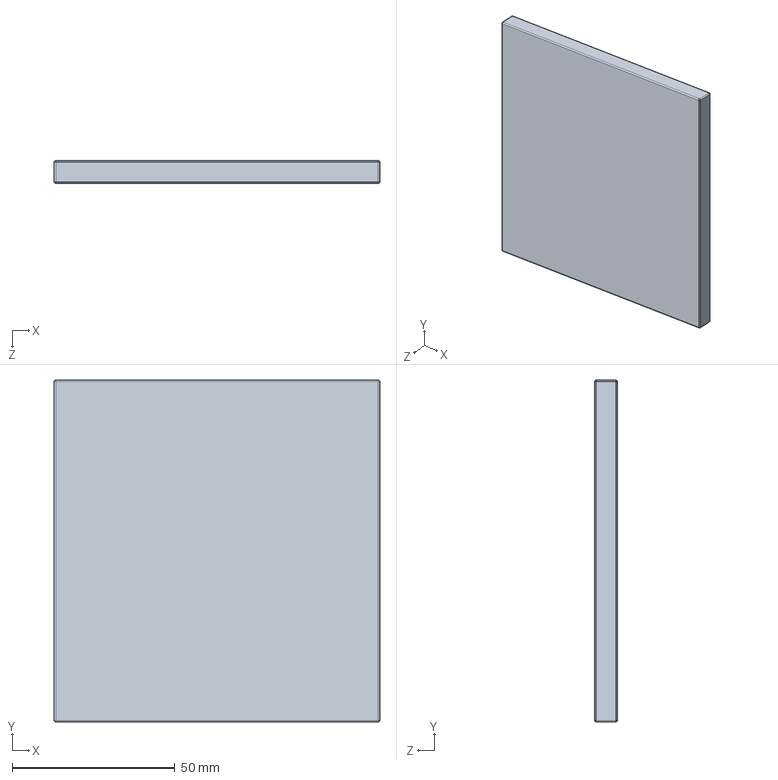
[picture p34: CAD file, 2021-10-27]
CAD/magneticsensorholder.SLDPRT
100.0 x 105.0 x 7.00 mm

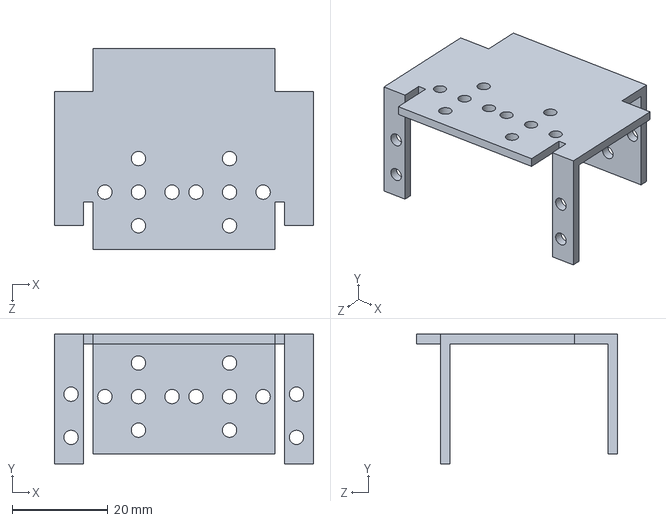
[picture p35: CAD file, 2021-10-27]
CAD/manipulator/servo mount.SLDPRT
54.0 x 27.0 x 42.0 mm

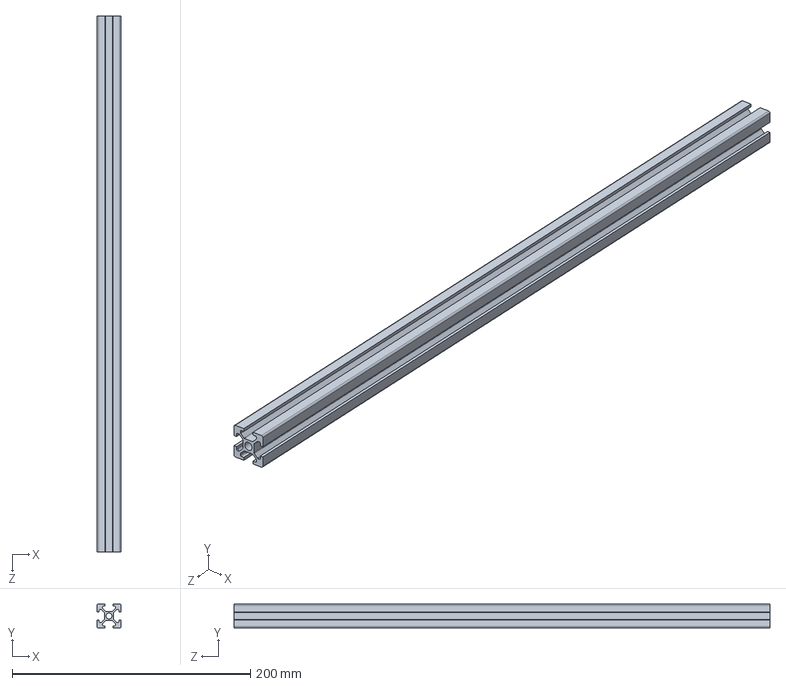
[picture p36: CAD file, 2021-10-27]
CAD/2020 alu section 450mm.SLDPRT
20.0 x 20.0 x 450.0 mm

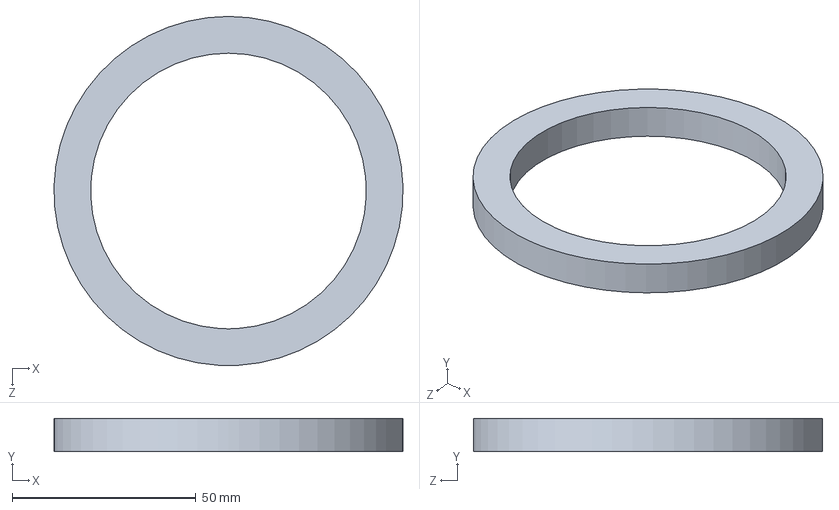
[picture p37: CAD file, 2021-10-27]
CAD/manipulator/large bearing.SLDPRT
95.0 x 9.00 x 95.0 mm

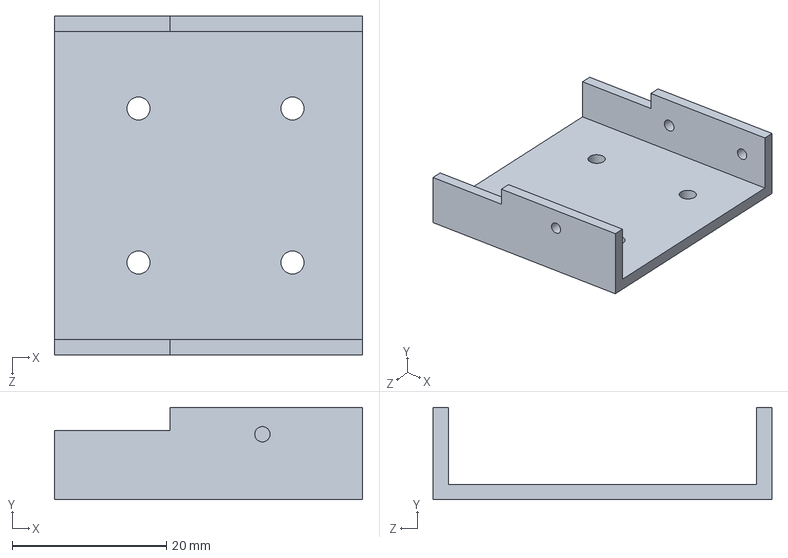
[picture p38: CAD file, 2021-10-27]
CAD/manipulator/base LDX-218 Servo Mount.SLDPRT
40.0 x 12.0 x 44.0 mm

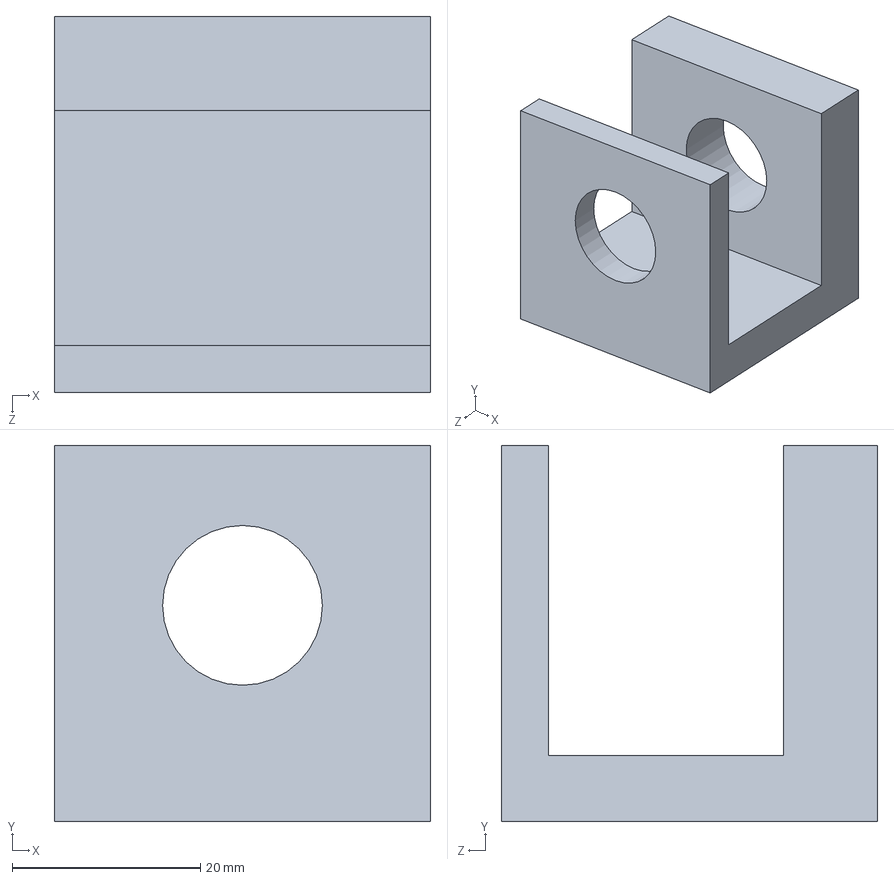
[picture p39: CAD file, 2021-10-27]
CAD/motorholder.SLDPRT
40.0 x 40.0 x 40.0 mm

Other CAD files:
CAD/2020 alu section 260mm.SLDPRT
CAD/manipulator/40 mm column.SLDPRT
CAD/2020 alu section 100mm.SLDPRT
CAD/manipulator/base ring.SLDPRT
CAD/180mm wheel.SLDPRT
CAD/2020 alu section 400mm.SLDPRT
CAD/2020 alu section 69mm.SLDPRT
CAD/2020 alu section 95mm.SLDPRT
CAD/2020 alu section.SLDPRT
CAD/2020 alu section150mm.SLDPRT
CAD/JQR03210-40ALCPU612.SLDPRT
CAD/JQR03210-40ALCPU612.dwg
CAD/base disk.SLDPRT
CAD/circuit board holder.SLDPRT
CAD/container base plate.SLDPRT
CAD/container wall with hole.SLDPRT
CAD/container wall.SLDPRT
CAD/largeBottomPlate.SLDPRT
CAD/manipulator/15mm column.SLDPRT
CAD/manipulator/9mm column.SLDPRT
CAD/manipulator/LDX-218 Digital Servo.SLDPRT
CAD/manipulator/bearing.SLDPRT
CAD/manipulator/drive gear.SLDPRT
CAD/manipulator/gripper base plate.SLDPRT
CAD/manipulator/gripper mount.SLDPRT
CAD/manipulator/gripper.SLDPRT
CAD/manipulator/lower base plate.SLDPRT
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

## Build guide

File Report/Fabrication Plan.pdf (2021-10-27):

# Farbrication Plan

## Fruit Picking Robot Group 7

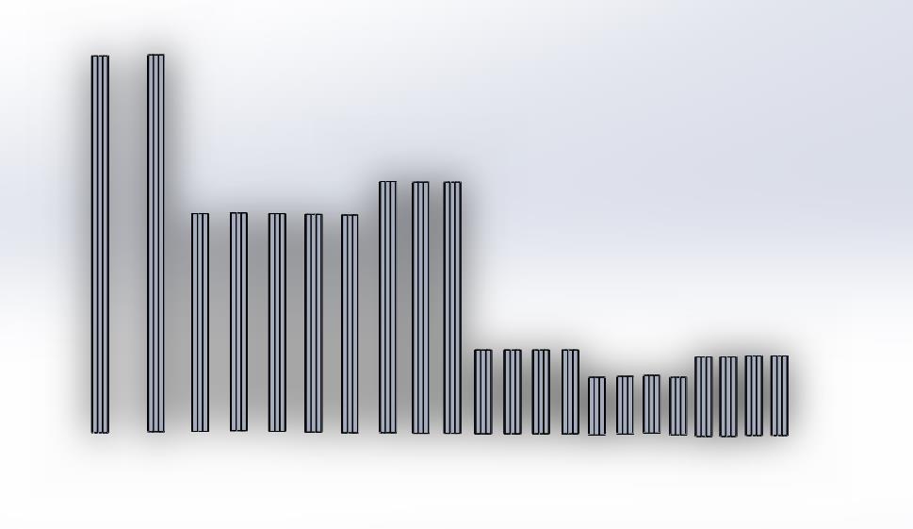
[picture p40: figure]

# Step 1

Cut purchased 2020 extruded aluminum beams to following different lengths with corresponding quantity:
450mm x2
300mm x3
260mm x5
100mm x4
95mm x4
70mm x4

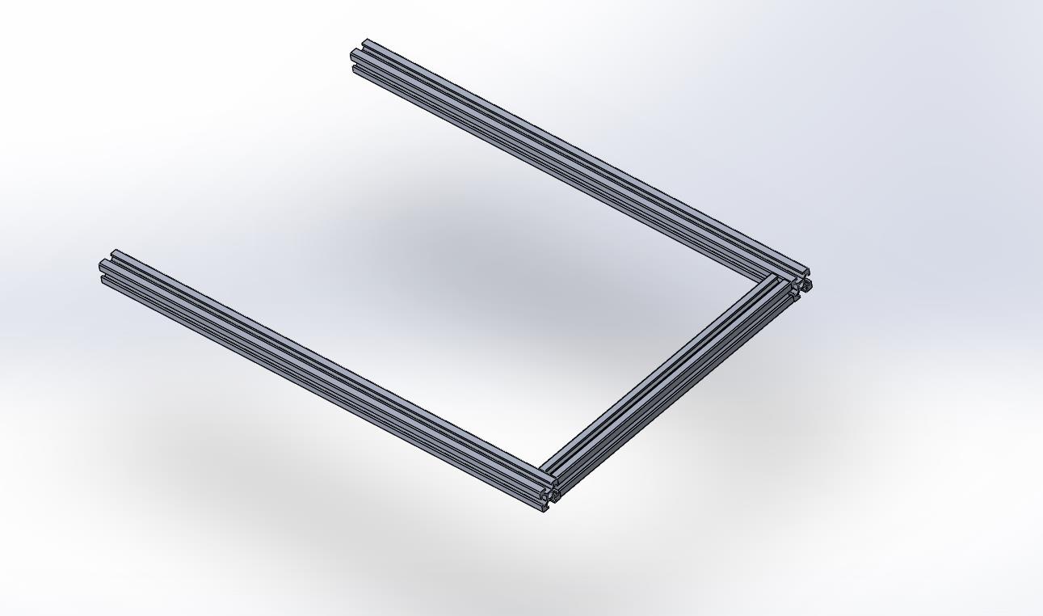
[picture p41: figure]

# Step 2

Starting with the base frame:
Connect two 450mm beam with a 260mm beam

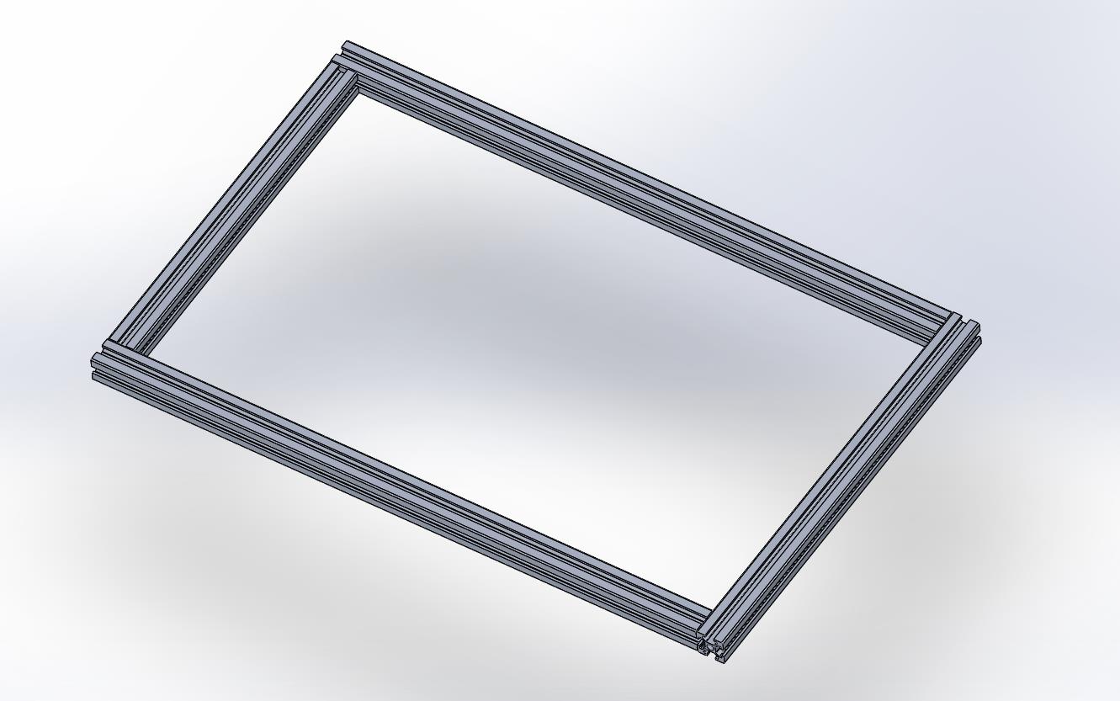
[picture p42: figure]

# Step 3

Connect the other end with a 300mm beam

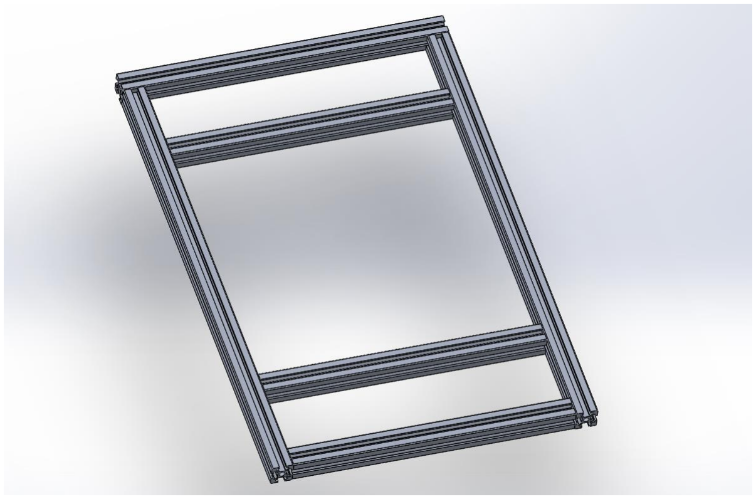
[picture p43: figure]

# Step 4

Add two 260mm beams in the middle of the frame, with a gap space of 260mm

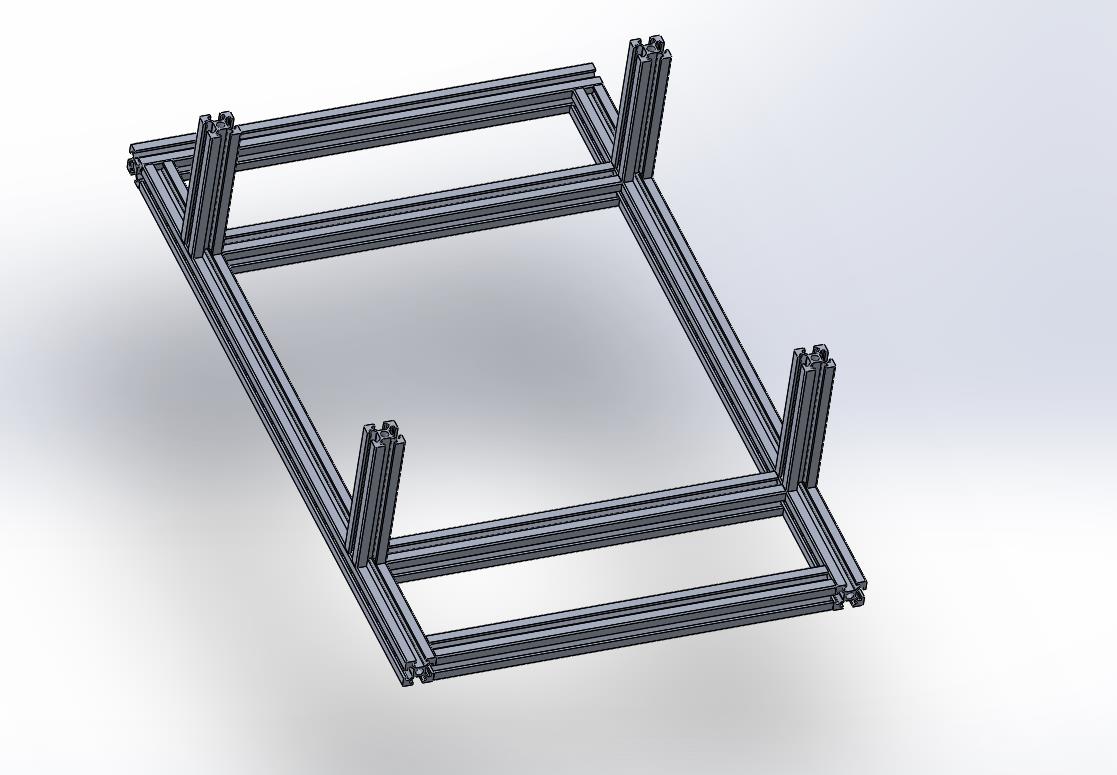
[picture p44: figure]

# Step 5

Now the assembly of the base frame is completed, starting the assembly of manipulator frame.
Connect four 100mm beam on each four corners of the inner rectangular frame.

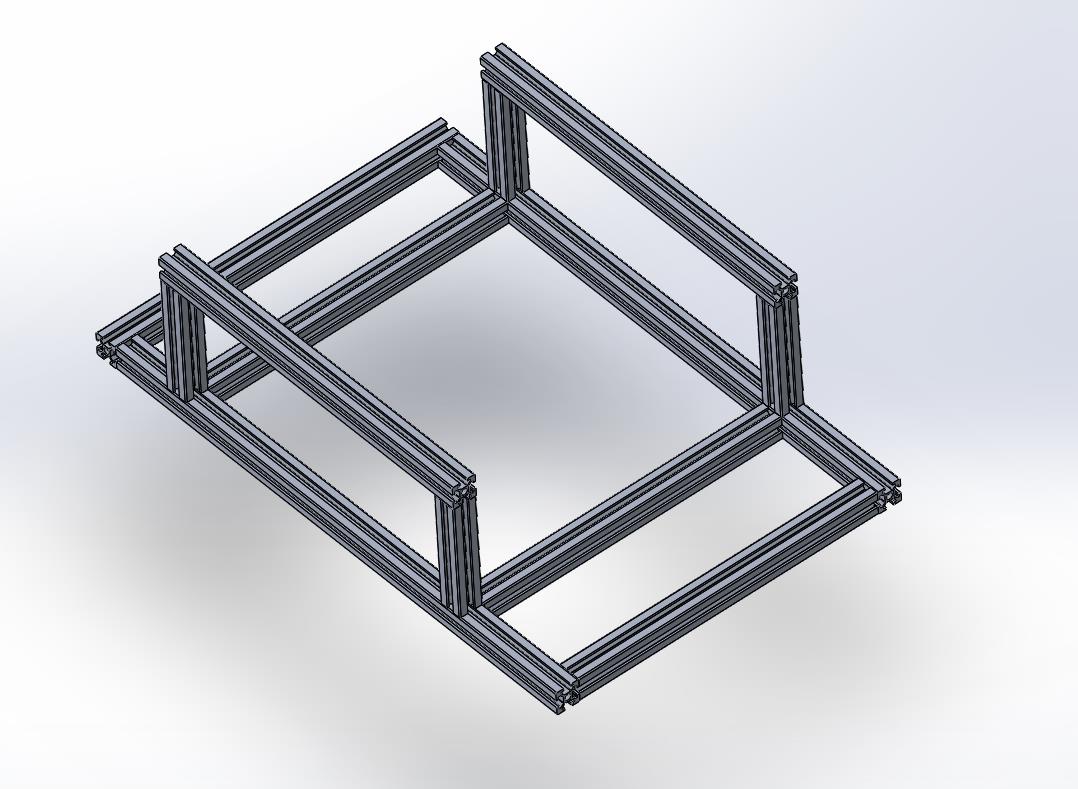
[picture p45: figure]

# Step 6

Connect two 300mm beams on the 100mm beams

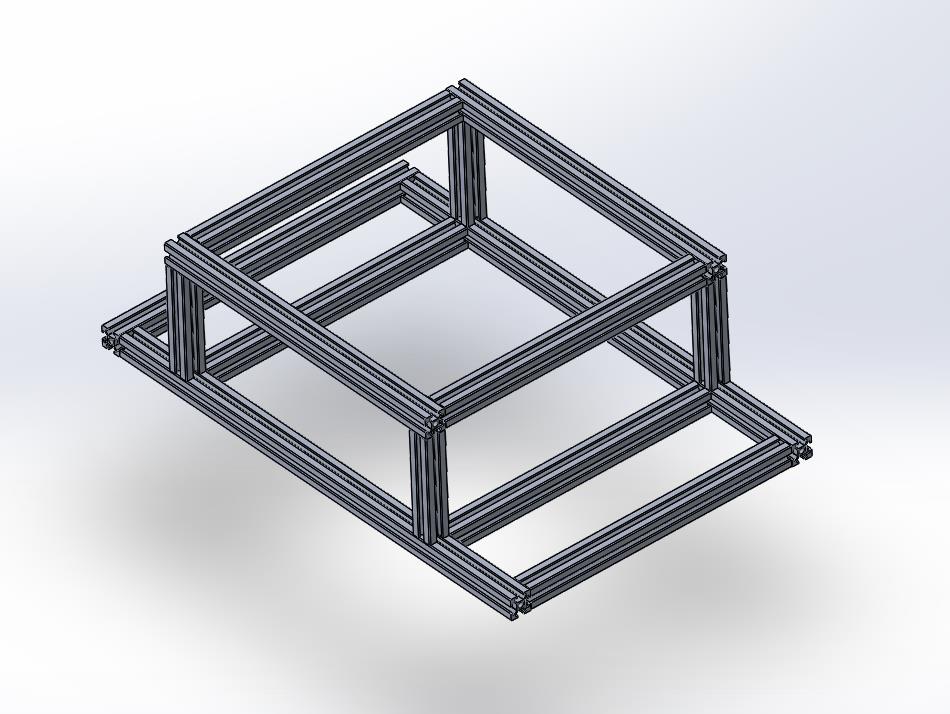
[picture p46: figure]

# Step 7

Connect two 260mm beams to the other side

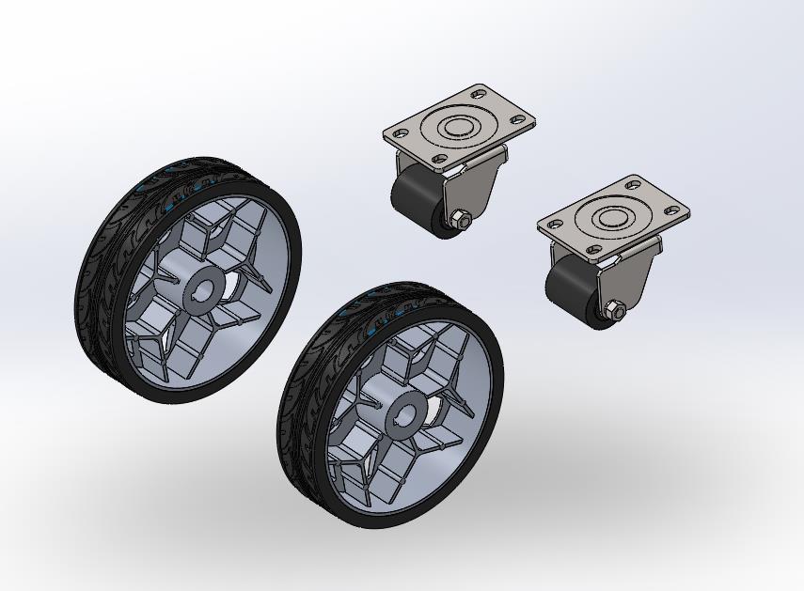
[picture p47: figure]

# Step 8

Now the assembly for general frame is finished, starting to attach wheels to the frame.
The wheels to be attached are listed as follow:
Two 1.6 inches driven wheels (caster) Two 180mm drive wheels with DC motor attached

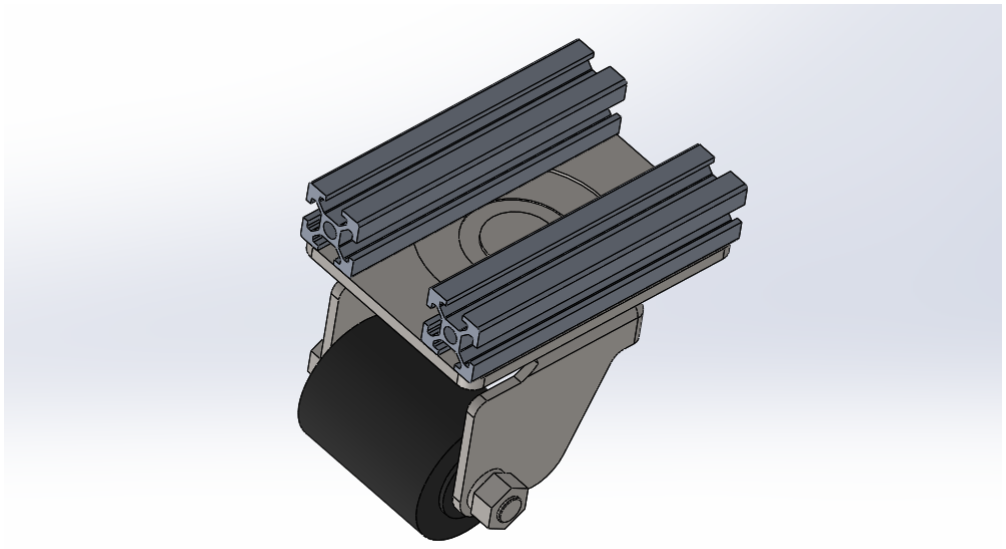
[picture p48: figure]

# Step 9

Attach the caster to two 95mm beam Repeat this step for the other caster.

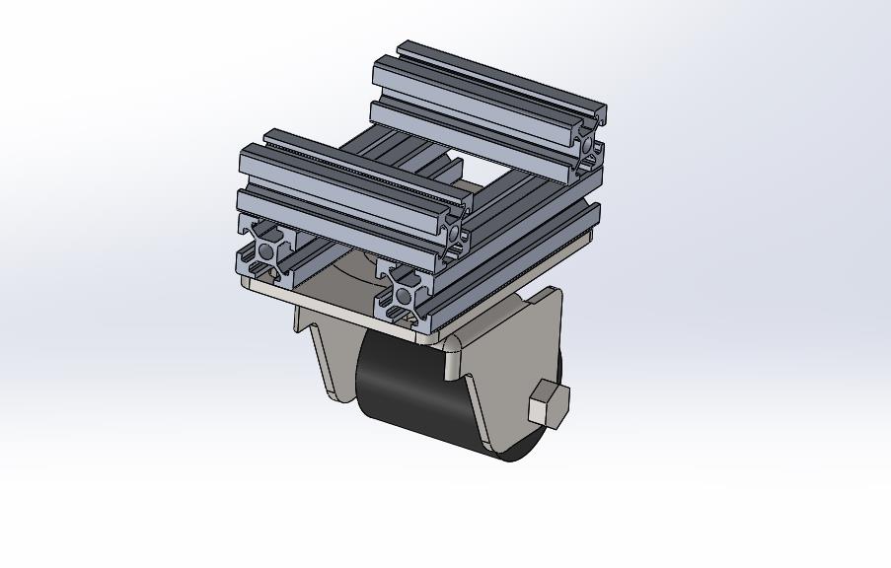
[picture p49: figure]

# Step 10

Attach the two 69mm beams on the 95mm beams
Repeat this step for the other caster.

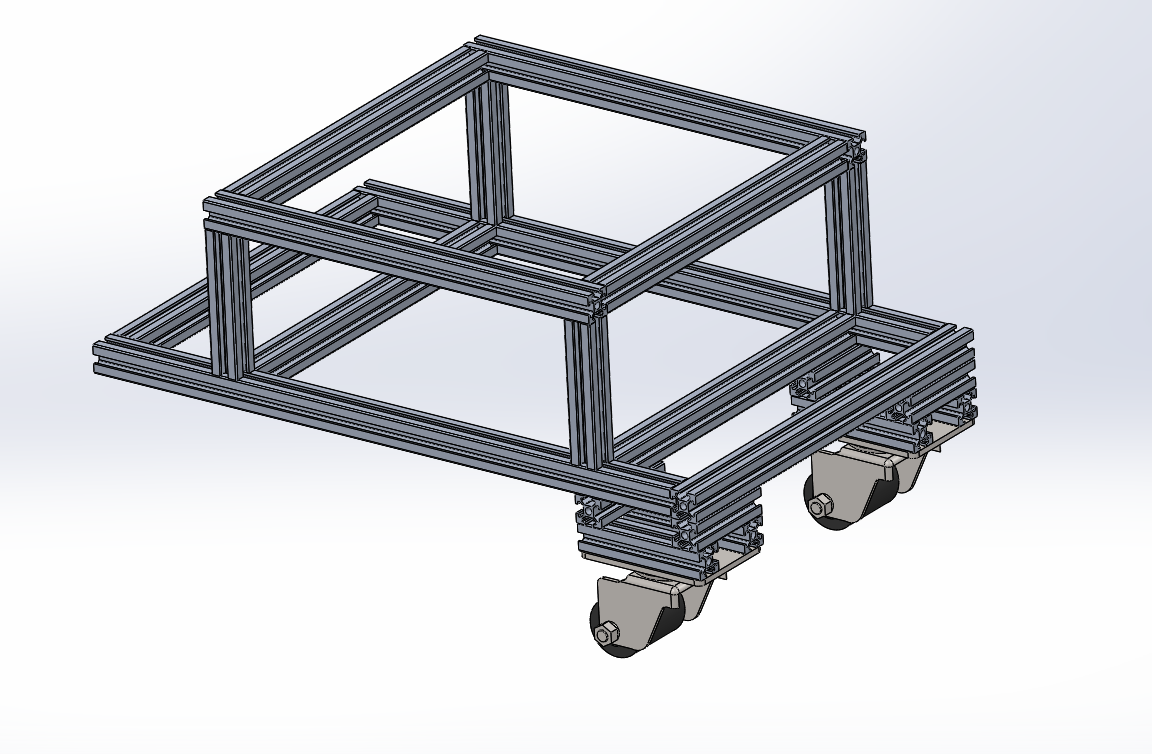
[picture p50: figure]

# Step 11

Attach these two caster to the frame as shown

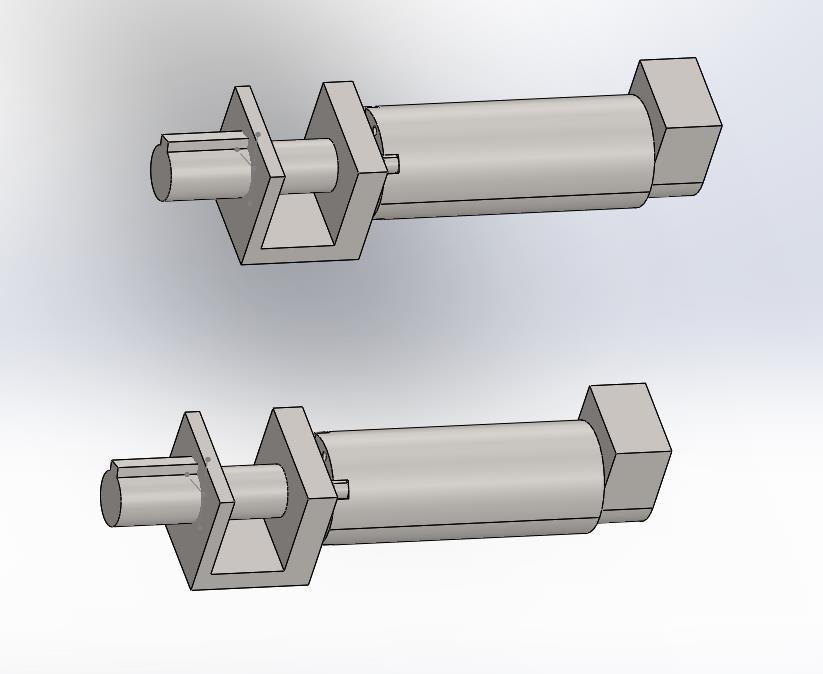
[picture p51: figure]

# Step 12

Obtain two DC motor with the motor mount

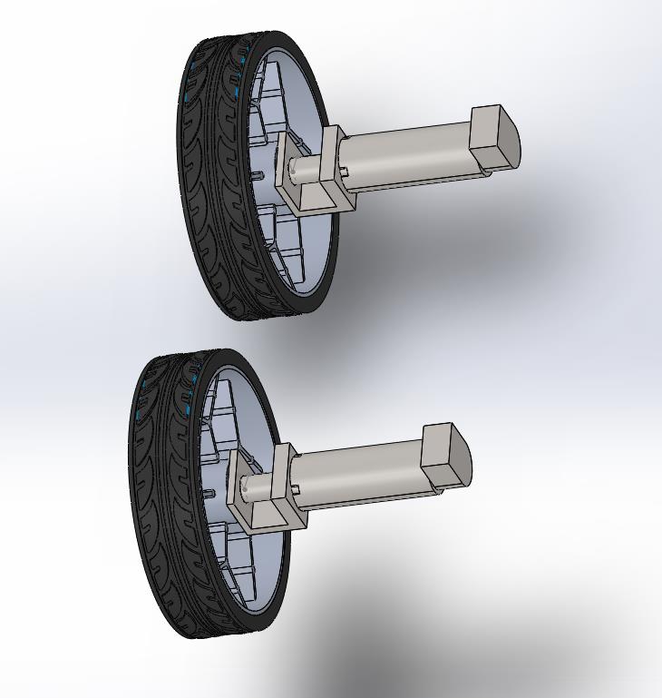
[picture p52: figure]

# Step 13

Attach wheels to the motor

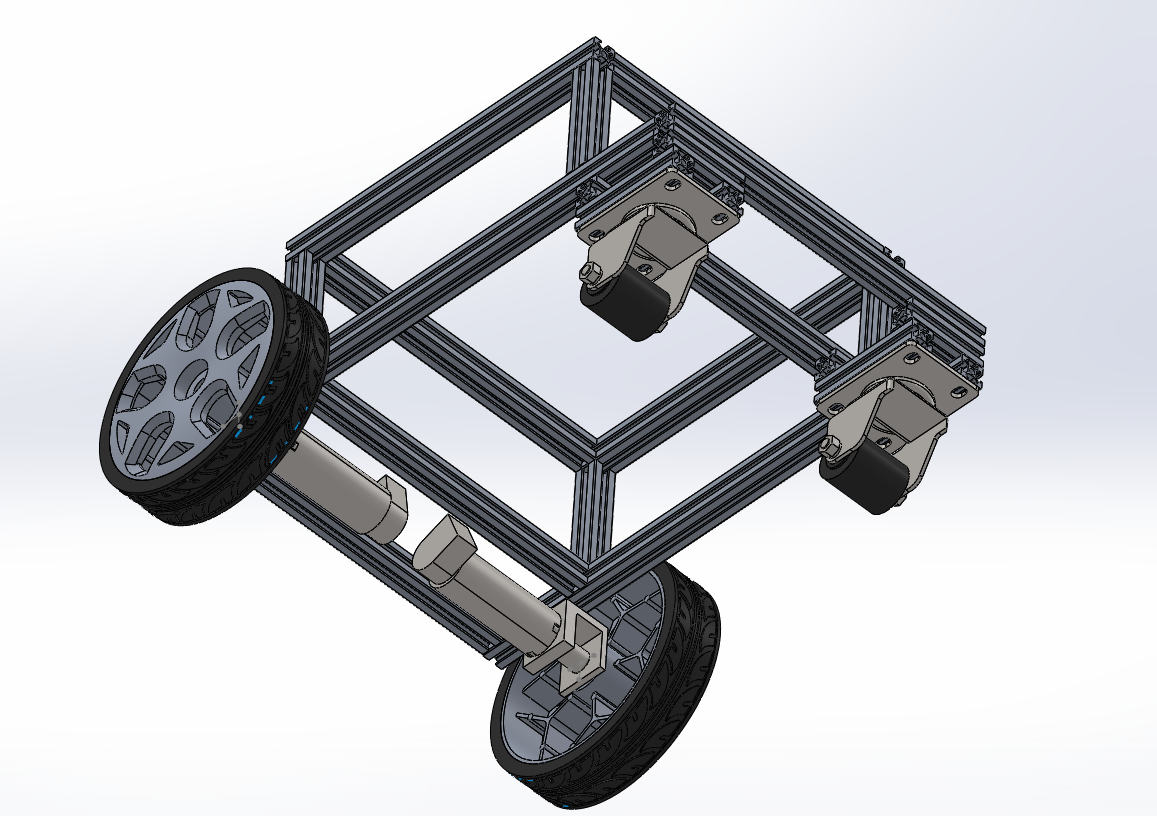
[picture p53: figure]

# Step 14

Attach the motor mount on the frame

# Step 14.A

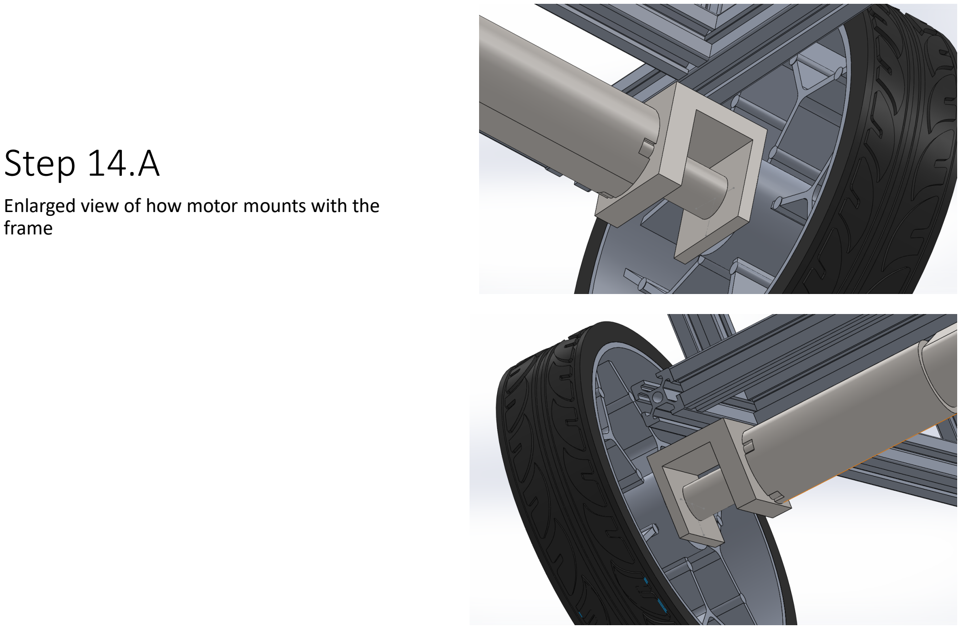
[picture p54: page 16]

Enlarged view of how motor mounts with the frame

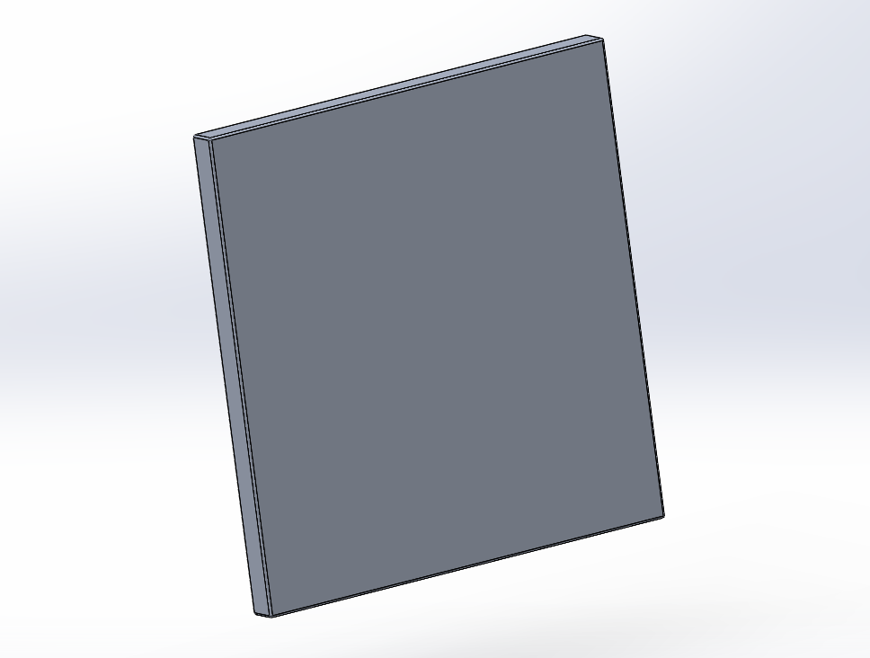
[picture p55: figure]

# Step 15

Fabricate an aluminum magnetic sensor holder plate that mounts in front of the frame.
Alternatives: Note that the material for holder has to be paramagnetic material (Aluminum, Stainless Steel etc.) to ensure that the magnetic sensor functions properly. The dimension for the holder fabricated: 100mm x 100mm x 7mm

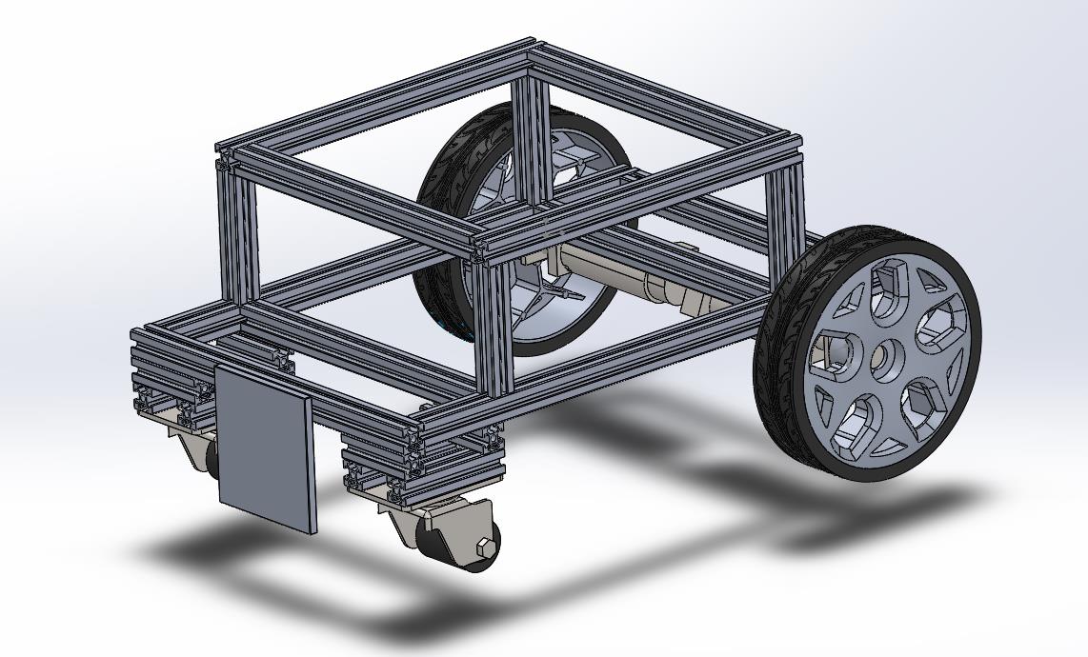
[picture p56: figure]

# Step 16

Place the sensor holder in the front of frame and make sure to mount the holder to be as centred as possible.

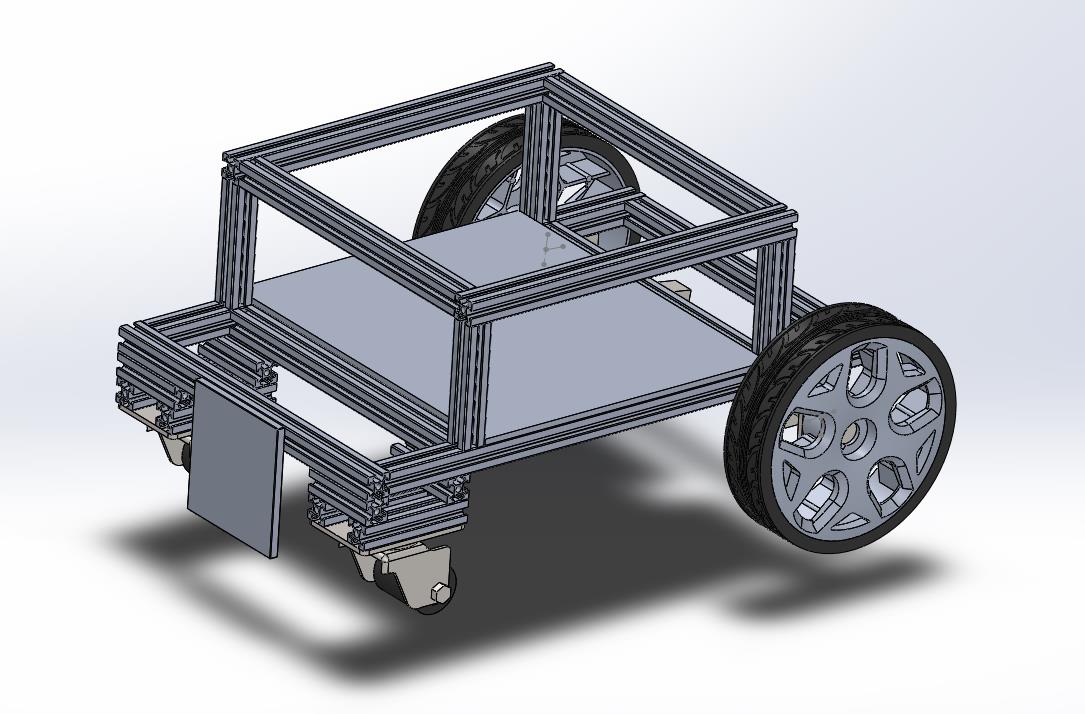
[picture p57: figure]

# Step 17

Mount a base plate of the dimensions: 300mm x 260mm x 3~6mm
Alternatives: Since the base plate holds the weight of fruit, it is recommended that to use material with higher strength, such as steel and aluminum.

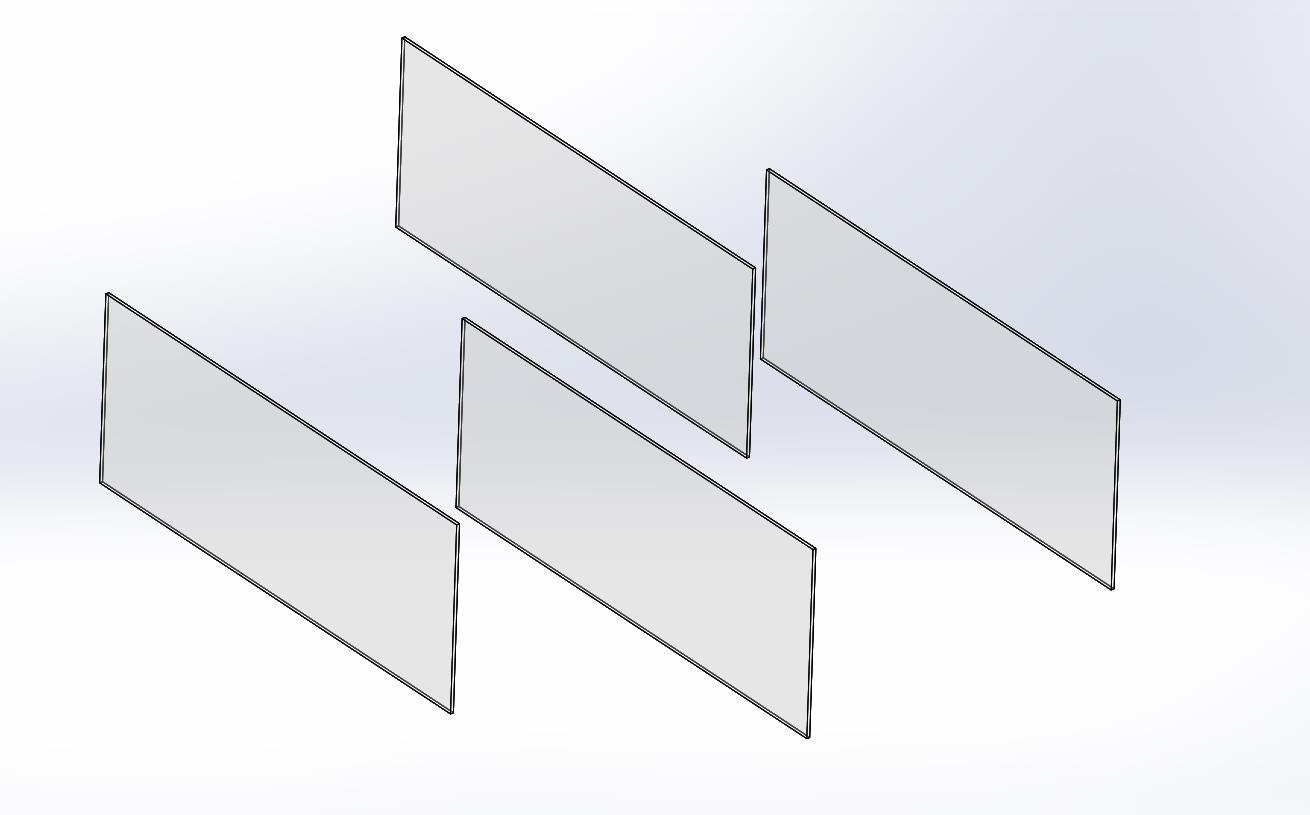
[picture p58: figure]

# Step 18

Fabricate four 300mm x 120mm x 2mm acrylic plates as the wall of the container.
Alternatives: The plate should be made out of transparent materials because of the users can tell if the container is full of not by inspection, such as high-strength tempered glass, polycarbonate (PC), polyethylene (PE) or acrylic.

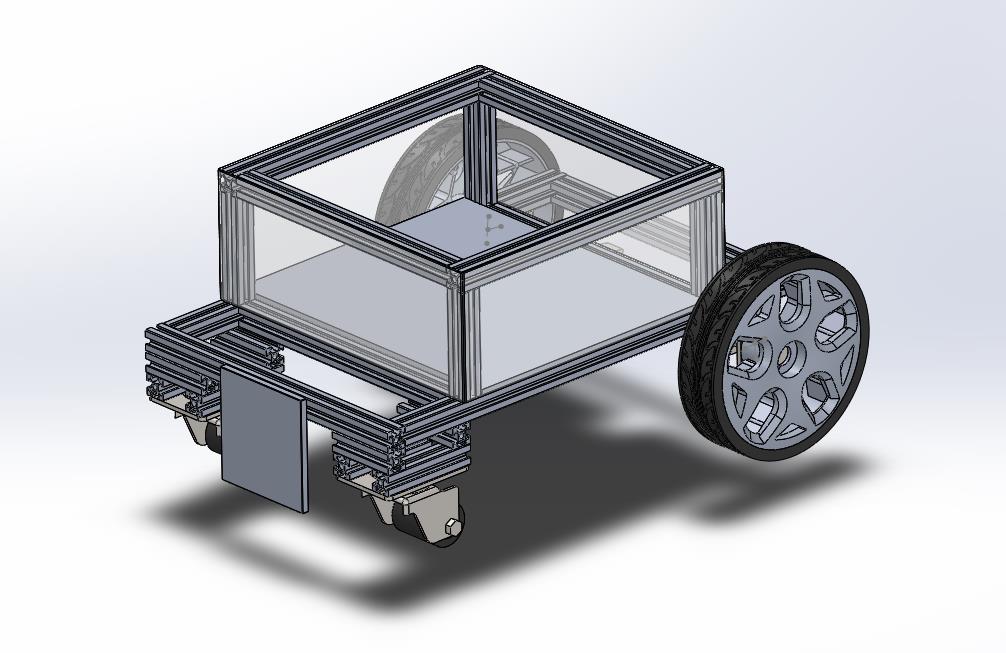
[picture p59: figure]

# Step 19

Mount these four acrylic plates on the side of central container

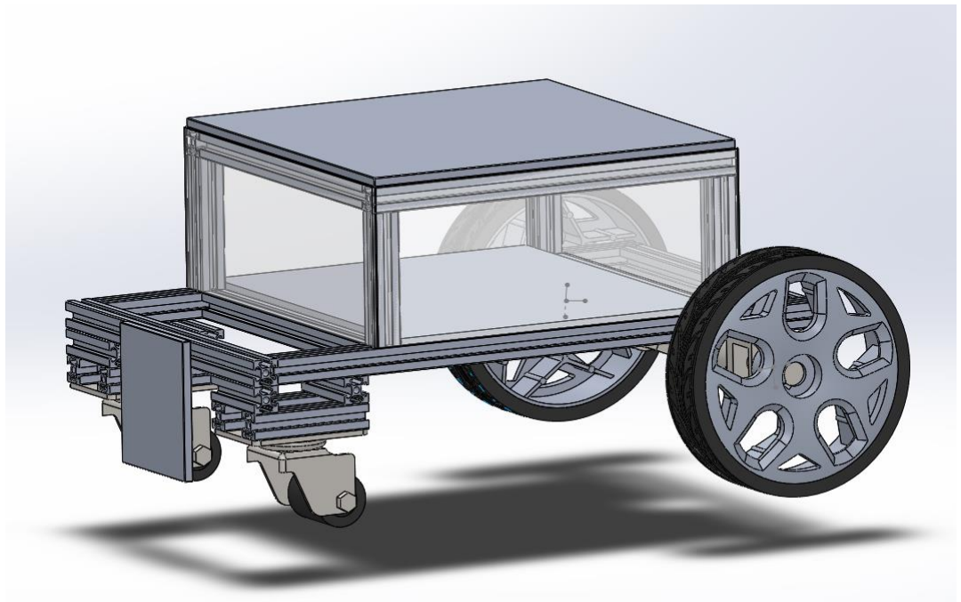
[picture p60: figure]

# Step 20

Mount a plate of 300mm x 300mm on top of the container as the base for manipulator Alternatives: The base plate will have to hold the weight of manipulator of approximately 1kg, so the strength of this plate do not to have be as high as the base plate, it can be made out of various materials.

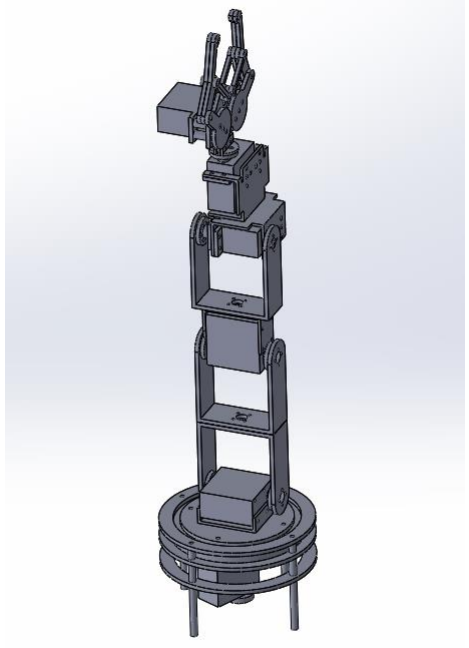
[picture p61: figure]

# Step 21

Mount the pre-purchased robotic manipulator on top of the container

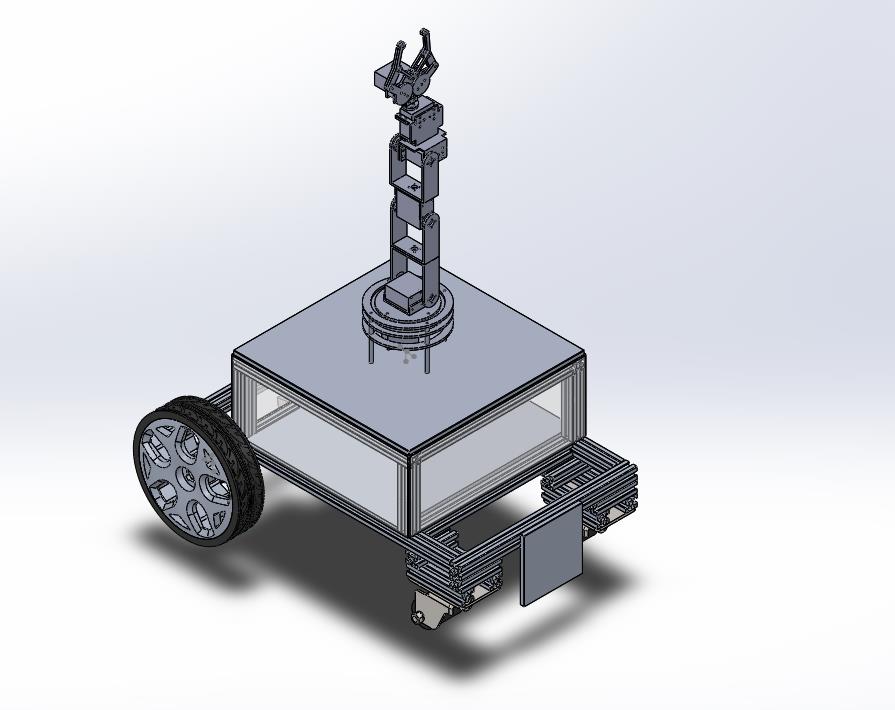
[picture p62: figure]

# Step 21.A

Manipulator should be mounted in the center of the base plate.

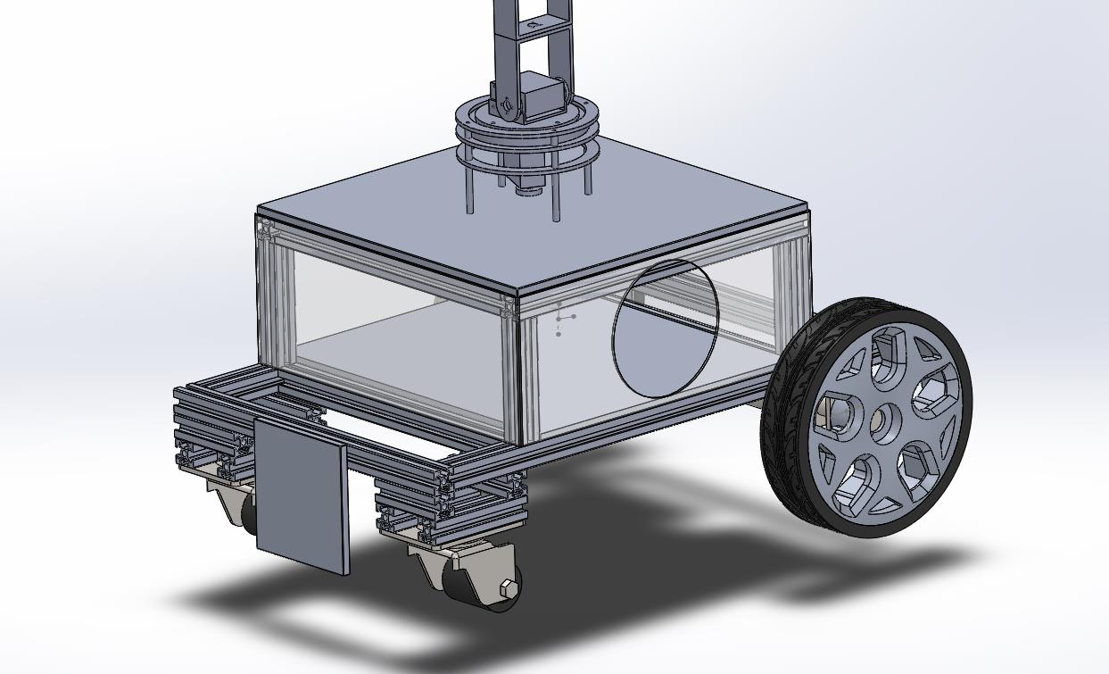
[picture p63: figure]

# Step 22

Make a hole of appropriate size on the left side acrylic plate, the dimension of the hole is depend on the size of transmission tube, since the size of different types of fruit is different, the size of transmission tube is a dependent factor.
The picture shown gave an example of the location of hole.

# Step 23

Connect the hole made in Step 22 and the end-effector of the manipulator with the transmission tube.

# Picture not available

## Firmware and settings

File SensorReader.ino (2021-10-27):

int sensor1Value = 0;
int sensor2Value = 0;
int sensor3Value = 0;
int sensor4Value = 0;
int sensor5Value = 0;
int sensor6Value = 0;
int sensor7Value = 0;
int sensor8Value = 0;
void setup() 
{
  Serial.begin(9600);
for (int i = 2; i <= 9; i++) pinMode(i, INPUT_PULLUP); // set pin 2-9 to input with pull up
}

void loop() {
 sensor1Value = digitalRead(2);
 sensor2Value = digitalRead(3);
 sensor3Value = digitalRead(4);
 sensor4Value = digitalRead(5);
 sensor5Value = digitalRead(6);
 sensor6Value = digitalRead(7);
 sensor7Value = digitalRead(8);
 sensor8Value = digitalRead(9);
  Serial.print(sensor1Value);
  Serial.print(sensor2Value);
  Serial.print(sensor3Value);
  Serial.print(sensor4Value);
  Serial.print(sensor5Value);
  Serial.print(sensor6Value);
  Serial.print(sensor7Value);
  Serial.print(sensor8Value);
  Serial.print("\n");
  delay(100);
}

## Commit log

2021-10-27 Fruit Picking Robot
    [15mm column.SLDPRT, 180mm wheel.SLDPRT, 2020 alu section 100mm.SLDPRT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]
2021-10-27 Driver code for navigation
